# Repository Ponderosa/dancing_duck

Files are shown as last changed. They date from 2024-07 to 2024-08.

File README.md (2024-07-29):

# Dancing Duck

This repo contains all software and tools for the Dancing Duck installation (title subject to change) for the Bumbershoot 2024 Festival. 

- Duck Firmware (Foundational work complete - RTOS, WiFi, MQTT Messaging, JSON interpretation, and Motor Control)
- Coordinator (Mosquitto is functionally passing motor command messages to duck)
- Monitor (No progress)

The design consists of ~20 motorized ducks that can be controlled to perform coordinated dance moves in the water. The ducks are decoys with an RC hobby boat mounted to the bottom. There are two DC brushed motor, each attached to a propeller. A custom PCBA will be manufactured that will feature the rPi Pico and a TI DRV33xx chip. The multicore RP2040 will be running SMP FreeRTOS and include LwIP and MQTT stacks. It will be able to interface with the Coordinator MQTT broker to receive motor commands, which will interface with a TI 83xx driver chip. Also included is a magnetometer to help ducks point in desired directions and to return to dock when needed.  

The ducks will be controlled via MQTT text based instructiones (JSON, G-Code, Something hand rolled?) being issued from the RPi4 Coordinator. The Coordinator will be running a broker, likely Mosquitto. Logging and monitoring infrastructure will be running on the Coordinator and may be accessed via a touchscreen mounted directly to the RPi4 or an external laptop known as the Monitor. 

# Duck Firmware
## Build Instructions
```
$ sudo apt update
$ sudo apt install cmake gcc-arm-none-eabi libnewlib-arm-none-eabi libstdc++-arm-none-eabi-newlib build-essential git
$ cd ~/workspace (or wherever you want to clone to)
$ git clone --recurse-submodules https://github.com/Ponderosa/dancing_duck.git
$ cd dancing_duck
$ git submodule update --init --recursive
$ cp wifi_example.sh wifi_secret.sh
$ vim wifi_secret.sh (add desired access point and MQTT broker information here)
$ ./build.sh <device_id>
```
Note: Please be careful not to commit any private wifi AP information.

For further Pico information, please see the getting started link below.

## Flashing Instructions
### Copy to mass storage via USB
The Pico can load firmware images by copying the U2F output file. It needs to put into mass storage mode first. To do this hold down the button on the pico while plugging in the USB cable. More instructions can be found in the getting started manual linked below.

### J-Link
1. Download and install latest package https://www.segger.com/downloads/jlink/ (Top section)
2. Solder 3 pins to Debug port on Pico and wire to SWD interface on J-Link.
3. Wire up hard reset pin to J-Link (Labeled "Run" on Pico)
4. Use flash.sh, ex `$ JLinkExe -ip 192.168.4.151 flash.sh`

### OpenOCD
Follow the getting started with Pico guide below.

## Debugging

### Serial Port
printf() is currently outputting to UART0 (GP0, GP1) at 3.3V. The UART is set to 115200-8-N-1. A lot of useful information is being streamed to this port. It is highly recommended to utilize this debug feature before venturing into GDB. 

Todo: Add build configuration file that can switch to USB CDC printf(). Or just move to USB CDC printf(). More details on CMakeLists modifications here: https://deepbluembedded.com/raspberry-pi-pico-serial-usb-c-sdk-serial-print-monitor/

### GDB
Since the rp2040 is dual core, care must be taken in properly attaching to the device. 

Included is a .vscode/launch.json to use with the VSCode plugin Cortex-Debug by marus25. Please feel free to add more configurations, as you probably don't have the same J-Link IP address I do. To get this to work start the Debug session directly from VSCode. You may need to reset the device one or two times with the left most reset button that appears in the new toolbar in the center top of VSCode. Once you do that, you should be able to use breakpoints and step through the code. 

Getting ARM GDB to run properly on Linux can be challenging. You may need to install older versions of libncurses and libncursesw

For my Ubuntu build this did the trick
```
sudo apt-get install libncurses5
sudo apt-get install libncursesw5
```

## Pico Documentation
- https://www.raspberrypi.com/documentation/microcontrollers/raspberry-pi-pico.html
- https://datasheets.raspberrypi.com/pico/getting-started-with-pico.pdf
- https://datasheets.raspberrypi.com/pico/raspberry-pi-pico-c-sdk.pdf
- https://datasheets.raspberrypi.com/rp2040/rp2040-datasheet.pdf

# Coordinator
1. Install https://mosquitto.org/download/ on RPi4.
2. edit `etc/mosquitto/conf.d/mosquitto.conf` and add 
```
allow_anonymous true
listener 1883 0.0.0.0
```
3. Run https://mqttx.app/ on any machine in the network for monitoring.

# MQTT Topics WIP
```
dancing_duck/
├── devices/
│   ├── {device_id}/
│   │   ├── sensors/
│   │   │   ├── temperature
│   │   │   ├── battery_voltage
│   │   │   └── ...
│   │   ├── metrics/
│   │   │   ├── freertos/
│   │   │   │   ├── heap
│   │   │   │   ├── tasks
│   │   │   │   └── ...
│   │   │   └── lwip
│   │   └── logs/
│   │   |   ├── info
│   │   |   ├── warning
│   │   |   └── error
│   │   └── command/
│   │   |   ├── motor
│   │   |   ├── navigate
│   │   |   ├── return_to_dock
│   │   |   ├── set_test_mode
│   │   |   └── ...
│   │   └── quack
│   └── ...
└── all_devices/
    ├── status
    └── command
        └── uart_tx
```

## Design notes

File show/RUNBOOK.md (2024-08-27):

# Bumbershoot 2024 Runbook

## Show

### Hook up phone to network
- Get wifi network and password from team lead once on site.
- Turn off 5G on phone (you will not have internet access or receive calls during this time)
- Visit http://192.168.42.2:3000/d/cdtmyrxqlji80b/duck-dance-party?orgId=1
- Get username and password from lead.
- Once done checking dashboards, re-enable 5G so you can operate your phone normally. 

### Stuck Duck
- If possible check propellers for fouling such as feathers, refuse, or others.
  - Gently remove fouling
  - Double check drain is secure plugged in
  - Return to water by pushing the duck off towards the center
- Check battery voltage for particular duck in Grafana dashboards
  - Disable 5G
  - Visit http://192.168.42.2:3000/d/cdtmyrxqlji80b/duck-dance-party?orgId=1
  - Scroll to "Duck - System" row
  - Select proper device
  - If below 4V (device 1 battery sense doesn't work)
    - Retrieve duck if posssible, remove batteries, and contatct team lead for debug
- If we are not receiving metrics from duck for more than 15 minutes and duck is not moving for more than 5 minutes
  -  Retrieve duck if possible, remove batteries, and contact team lead for debug

### Wind clumping
1. Enable wind correction with CLI
  1. Identify wind direction
  2. `python3 duck_mqtt_cli.py wind_on -d <direction of wind in degrees> -t <time in seconds to correct for wind> -i <interval in seconds>`
  3. Try using launch time for duration and 5 to 15 minutes for interval

## Setup
### Pre-show Preperation
1. Take a picture of each duck with respective boat for debugging
1. Enable hotspot on phone to synchronize rpi4 clock 
1. Enable power to command station
1. Wait for wi-fi to initialize
1. Log into Grafana to check rpi4 metrics
1. Calibrate and launch all ducks
1. SSH into server and start show
   1. `cd workspace/dancing_duck/show`
   1. `./run_show.sh`

### Duck Launch
1. Add fresh batteries to boat and secure battery cover
1. Setup boat on calibration platform
1. Use CLI to send calibration command 
   1. `cd show`
   2. `python3 duck_mqtt_cli.py device <n> calibrate`
   3. Rotate boat slowly on calibration platform
1. Attach duck decoy to boat
1. Launch Duck
   1. Place duck in water
   1. Identify heading towards center of pool
   1. `python3 duck_mqtt_cli.py device <n> launch --heading <0-359> --launch_time <10-100>`
   1. Adjust launch time on next duck to approximately get to center of pool

### Teardown
1. Remove all batteries from all duck and place each set of batteries in it's own baggie.

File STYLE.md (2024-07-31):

## File Format
- Use format on save.
- The .clang-format file found in this directory will be used.
- It uses the Google style with longer line limits and some macro readability improvements. 
- This file is not set in stone, please feel free to suggest updates.
- Do not let a file length exceed 1000 lines. Consider refactor at 500 lines.

## Parenthesis
- Use them everywhere. Assume the other person reading the code doesn't know operator precedence. 

## Keywords to frequent
- static
- const
- volatile (where appropriate)
- double (avoid 32-bit float issues)

## Typedefs
- Generally avoid typedefs
- Do not use for structs or enums
- Allowed for fixed width integer types (more below)

## Interger representation
- Use fixed width integer type almost always. Ex `uint32_t foo = 42;`
- Use fixed width macros for string formatting. Ex `printf("Number: %" PRIu32 "\n", number);`
- Using `int` is fine for loops unless you are explictly relying on the rollover

## String formatting
- All string formatting will use `snprintf()` unless there is a good reason not to.
- Exception: using printf is fine for simple string formatting.

## Functions
- Generally keep functions less than 50 lines
- Exception: Long case statements, where each case is only a couple lines of code
- Keep local variable to less then 5~10
- Keep indentation level low. Invert your logic and split your loops if needed. 

## Function Prototypes
- Keep variable names and types

## Early exits and jumps
- Try to only have one return statement per function. There are exceptions.
- When using early exits or jumps clearly label where they happen in code
- Give jumps descriptive names
- Note: Jumps are usually for cleaning up memory allocation for early exits

## Braces
- Always use them, even for one line if statements

## Commenting
- Describe What code does, sometimes Why, and not How it works.
- Describe all public interfaces in header files
- Do not comment out large sections of code, if needed for testing wrap in if statement and add config variable
- Todo: Should this project use doxygen type comments?

## Macros
- Avoid `#define constant`, and use `static type name = val` instead.
- Use enums when defining related constants
- Macros with multiple statements should use a do while loop to protect them
- Macros should not effect control flow (very bad)
- Functions are preferred to macros if equivelency can be made

## Naming 
- Use descriptive naming for any global variables or interfaces
- Use descriptive naming when in doubt
- Exceptions are loop counters and internal variables to short functions
- Excpetion: Anytime when interacting with library, such as FreeRTOS, the naming convention of that library may bleed into this project. We are working with multiple libraries and cannot just inherit one style.

### Modules
- .c and .h files should be snake case (all_lower_case_with_underscores)

### Functions
- Functions should snake case (all_lower_case_with_underscores)
- Functions returning a value with units should be postfixed with the unit they are returning i.e. `uint32_t get_time_ms()`
- Exception: FreeRTOS task functions shall follow FreeRTOS naming conventions `vFreeRTOSTask`

### Types
- For enums, structs, typedefs(used judicially), etc, use upper camel case (UpperCamelCase)

### Macros
- If you absolutely have to use a macro, use UPPER_CASE naming convention

### Static Const for #define replacement
- Same as macros, UPPER_CASE

### Variables
- All variable names shall use snake_case unless otherwise called out below
- enum variables shall use the UPPER_CASE naming convention, make sure you don't create collisions with macros
- Variables should always end with their units if they are a measure of something (`float magnetic_flux_uT = 0;` - micro Tesla)
- Capital letters are allowed for units. For very common units like seconds, keep them lower case.
- Prefix gloabl variables with global `char global_mac_address[32]`
- Try to avoid use of global variables.

## Allocating memory
- The FreeRTOS memory allocator is preferred.

## Casting
- Cast away from void* as soon as possible
- If casting, ask yourself if the original type should change 

## Zeroing memory
- use {0} when defining, otherwise use memset

## Early optimization
- Don't inline functions unless you have data to support it's use
- If the task stack watermark is less than half, make it larger
  - Exception: We start to approach 70% max heap usage watermark
- Only use floats, instead of doubles, if optimization calls for it
- Only use fixed point math if optimization calls for it

## Conditional Compilation
- Try to avoid in general
- Leave a comment at the end of #endif 

## Resetting the device and panicking
- Try to avoid this and fail gracefully
- Exceptions, if we can not connect to wi-fi we are dead in the water.
  - Todo: consider auto return to dock if we loose wi-fi after multiple reboots and still have the compass

## Inspriation for this Guide
- Personal Experience - Style guides are highly opinionated
- Linux kernel coding style https://www.kernel.org/doc/html/latest/process/coding-style.html
- Barr's Embedded C Coding Standard https://barrgroup.com/embedded-systems/books/embedded-c-coding-standard
- Ben Klemens, 21st Century C
- Google C++ Style Guide https://google.github.io/styleguide/cppguide.html

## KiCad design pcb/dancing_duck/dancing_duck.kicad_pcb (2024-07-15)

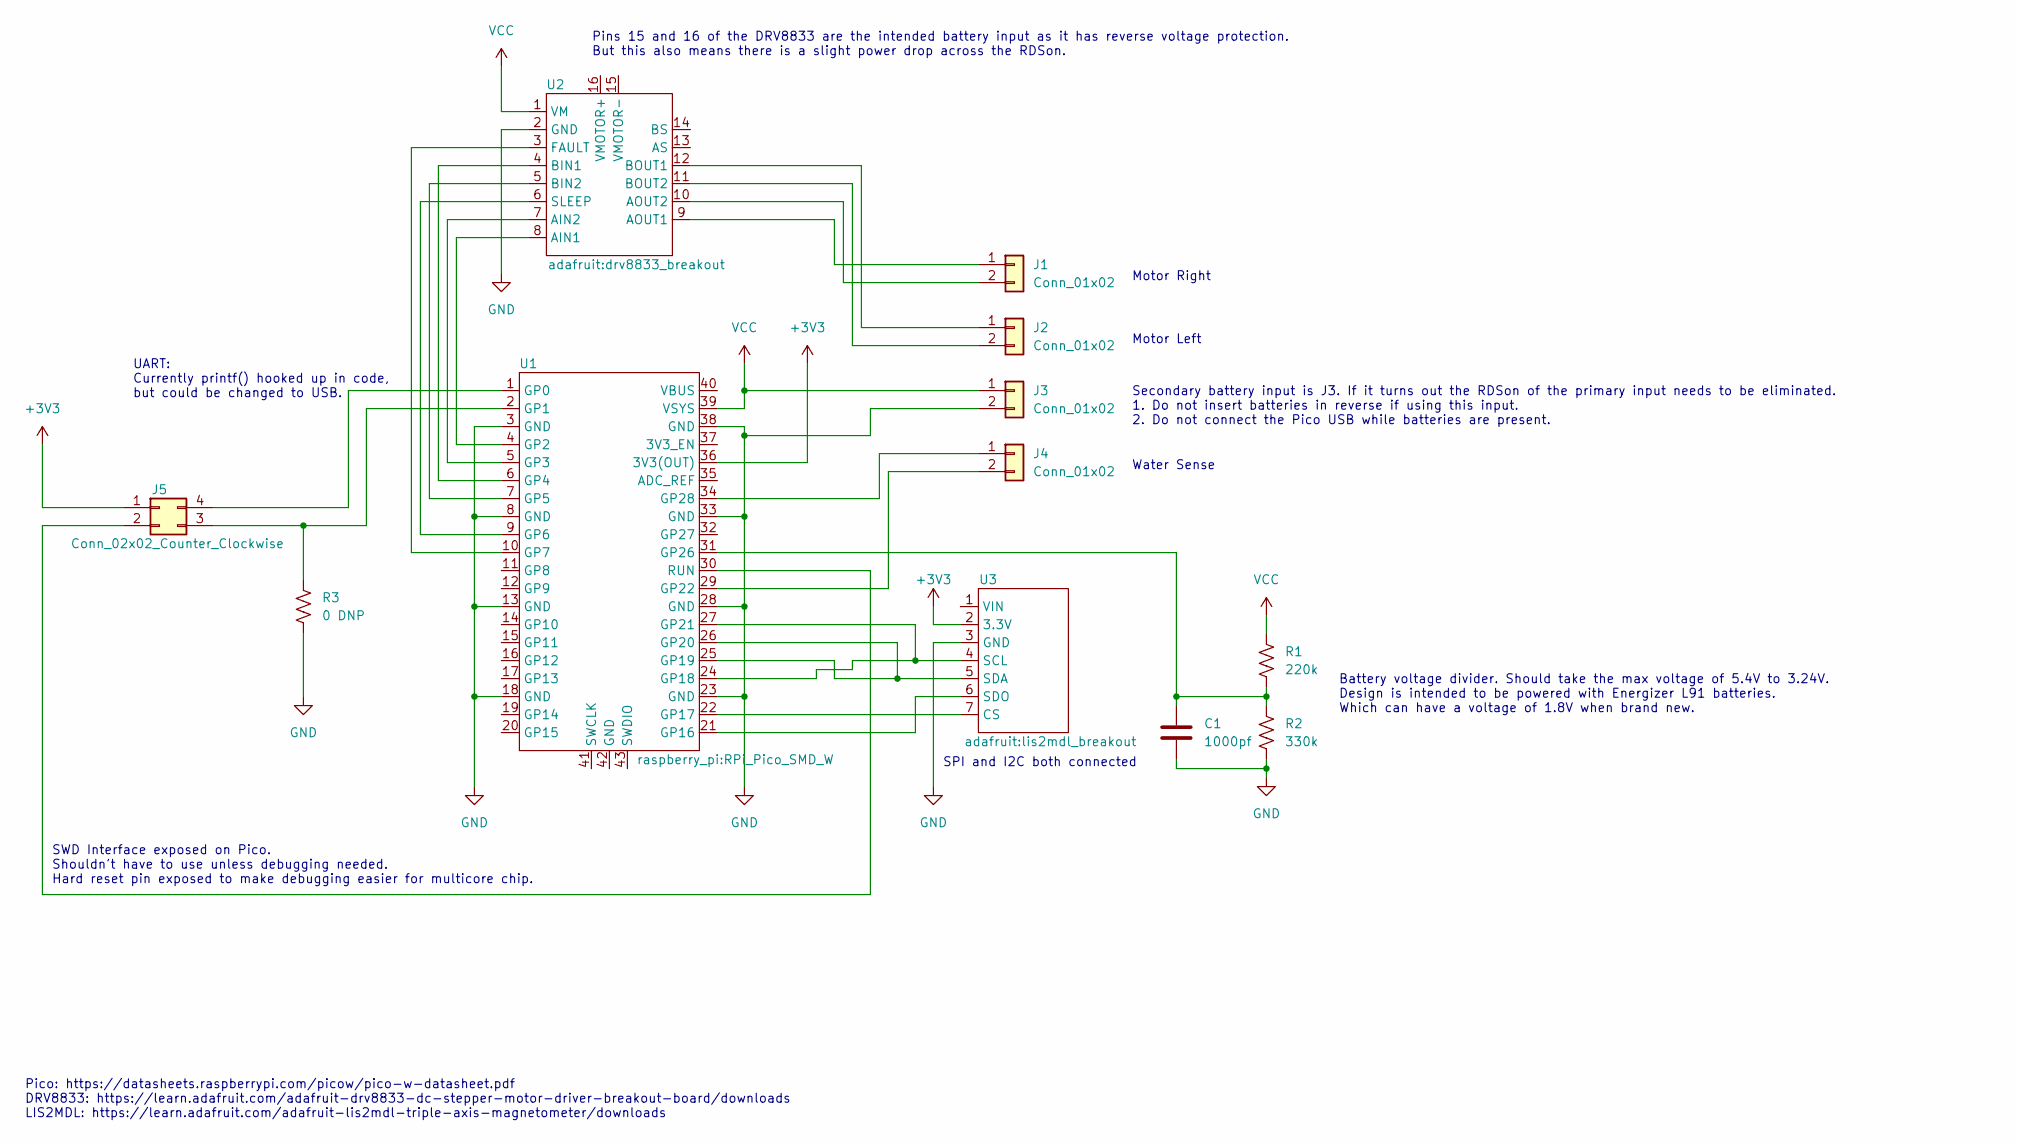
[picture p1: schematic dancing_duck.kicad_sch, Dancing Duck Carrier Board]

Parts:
C1: 1000pf; C_1206_3216Metric_Pad1.33x1.80mm_HandSolder; Part Num CL31B102KGFNNNE
J1, J2, J4: Conn_01x02; JST_PH_S2B-PH-K_1x02_P2.00mm_Horizontal
J3: Conn_01x02; TerminalBlock_Phoenix_PT-1,5-2-3.5-H_1x02_P3.50mm_Horizontal
J5: Conn_02x02_Counter_Clockwise; PinHeader_2x02_P2.54mm_Vertical
R1: 220k; R_1206_3216Metric_Pad1.30x1.75mm_HandSolder
R2: 330k; R_1206_3216Metric_Pad1.30x1.75mm_HandSolder
R3: 0 DNP; SolderJumper-2_P1.3mm_Open_TrianglePad1.0x1.5mm
U1: RPi_Pico_SMD_W
U2: drv8833_breakout
U3: lis2mdl_breakout

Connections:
+3V3: J5.1, U1.36 (3V3(OUT)), U3.2 (3.3V)
GND: C1.2, J3.2, R2.2, R3.2, U1.3 (GND), U1.8 (GND), U1.13 (GND), U1.18 (GND), U1.23 (GND), U1.28 (GND), U1.33 (GND), U1.38 (GND), U2.2 (GND), U3.3 (GND)
unnamed: J1.1, U2.9 (AOUT1)
unnamed: J1.2, U2.10 (AOUT2)
unnamed: J2.1, U2.12 (BOUT1)
unnamed: J2.2, U2.11 (BOUT2)
unnamed: J4.1, U1.34 (GP28)
unnamed: J4.2, U1.29 (GP22)
unnamed: J5.2, U1.30 (RUN)
unnamed: J5.3, R3.1, U1.2 (GP1)
unnamed: J5.4, U1.1 (GP0)
unnamed: U1.4 (GP2), U2.8 (AIN1)
unnamed: U1.5 (GP3), U2.7 (AIN2)
unnamed: U1.6 (GP4), U2.4 (BIN1)
unnamed: U1.7 (GP5), U2.5 (BIN2)
unnamed: U1.9 (GP6), U2.6 (SLEEP)
unnamed: U1.10 (GP7), U2.3 (FAULT)
unnamed: U1.21 (GP16), U3.6 (SDO)
unnamed: U1.22 (GP17), U3.7 (CS)
unnamed: U1.24 (GP18), U1.27 (GP21), U3.4 (SCL)
unnamed: U1.25 (GP19), U1.26 (GP20), U3.5 (SDA)
unnamed: C1.1, R1.2, R2.1, U1.31 (GP26)
VCC: J3.1, R1.1, U1.39 (VSYS), U2.1 (VM)

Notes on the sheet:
Motor Right
Motor Left
Secondary battery input is J3. If it turns out the RDSon of the primary input needs to be eliminated. 1. Do not insert batteries in reverse if using this input. 2. Do not connect the Pico USB while batteries are present.
Water Sense
Pico: https://datasheets.raspberrypi.com/picow/pico-w-datasheet.pdf DRV8833: https://learn.adafruit.com/adafruit-drv8833-dc-stepper-motor-driver-breakout-board/downloads LIS2MDL: https://learn.adafruit.com/adafruit-lis2mdl-triple-axis-magnetometer/downloads
Battery voltage divider. Should take the max voltage of 5.4V to 3.24V. Design is intended to be powered with Energizer L91 batteries. Which can have a voltage of 1.8V when brand new.
UART: Currently printf() hooked up in code, but could be changed to USB.
Pins 15 and 16 of the DRV8833 are the intended battery input as it has reverse voltage protection. But this also means there is a slight power drop across the RDSon.
SPI and I2C both connected
SWD Interface exposed on Pico. Shouldn't have to use unless debugging needed. Hard reset pin exposed to make debugging easier for multicore chip.

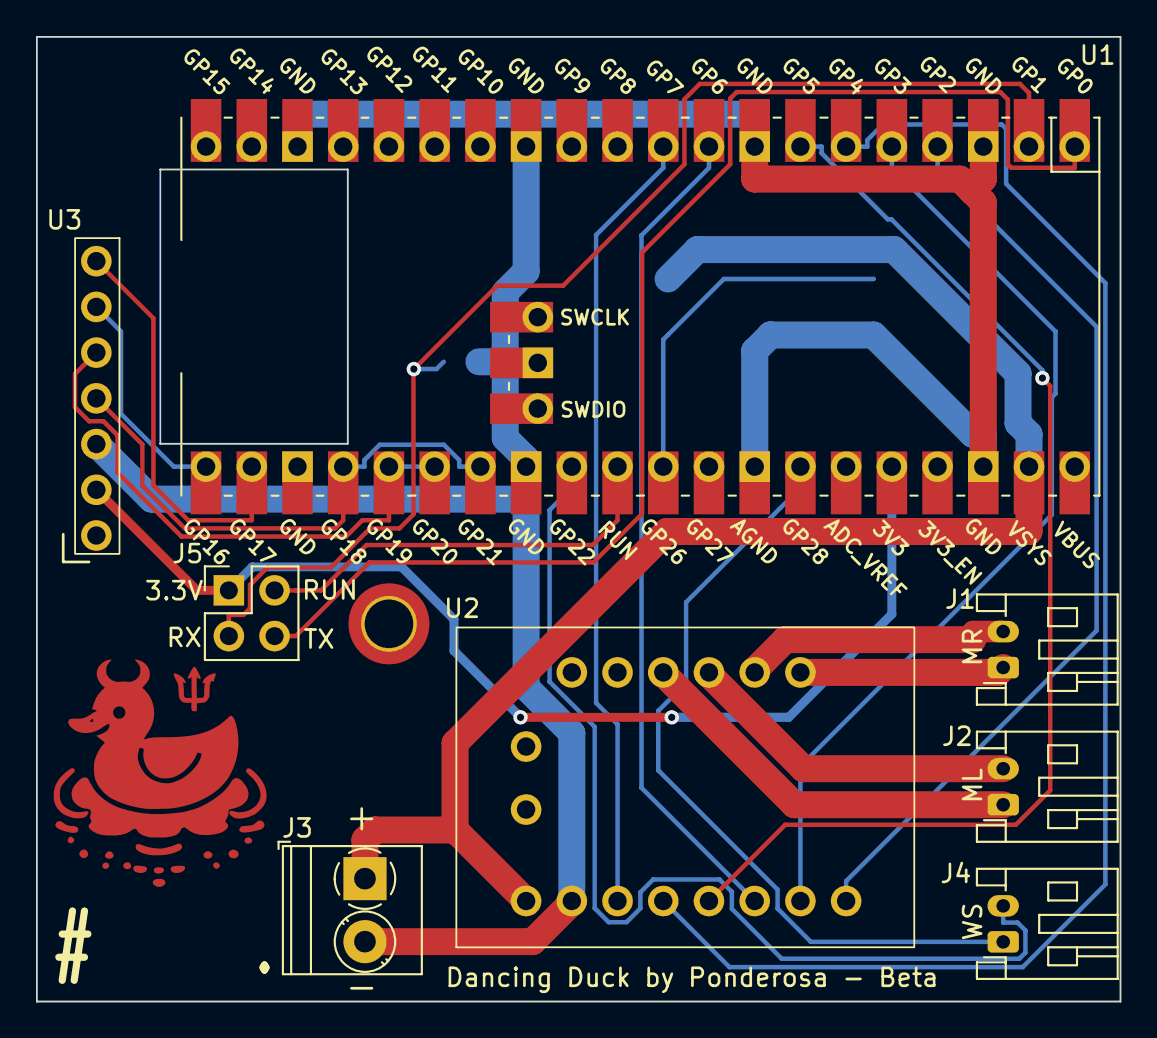
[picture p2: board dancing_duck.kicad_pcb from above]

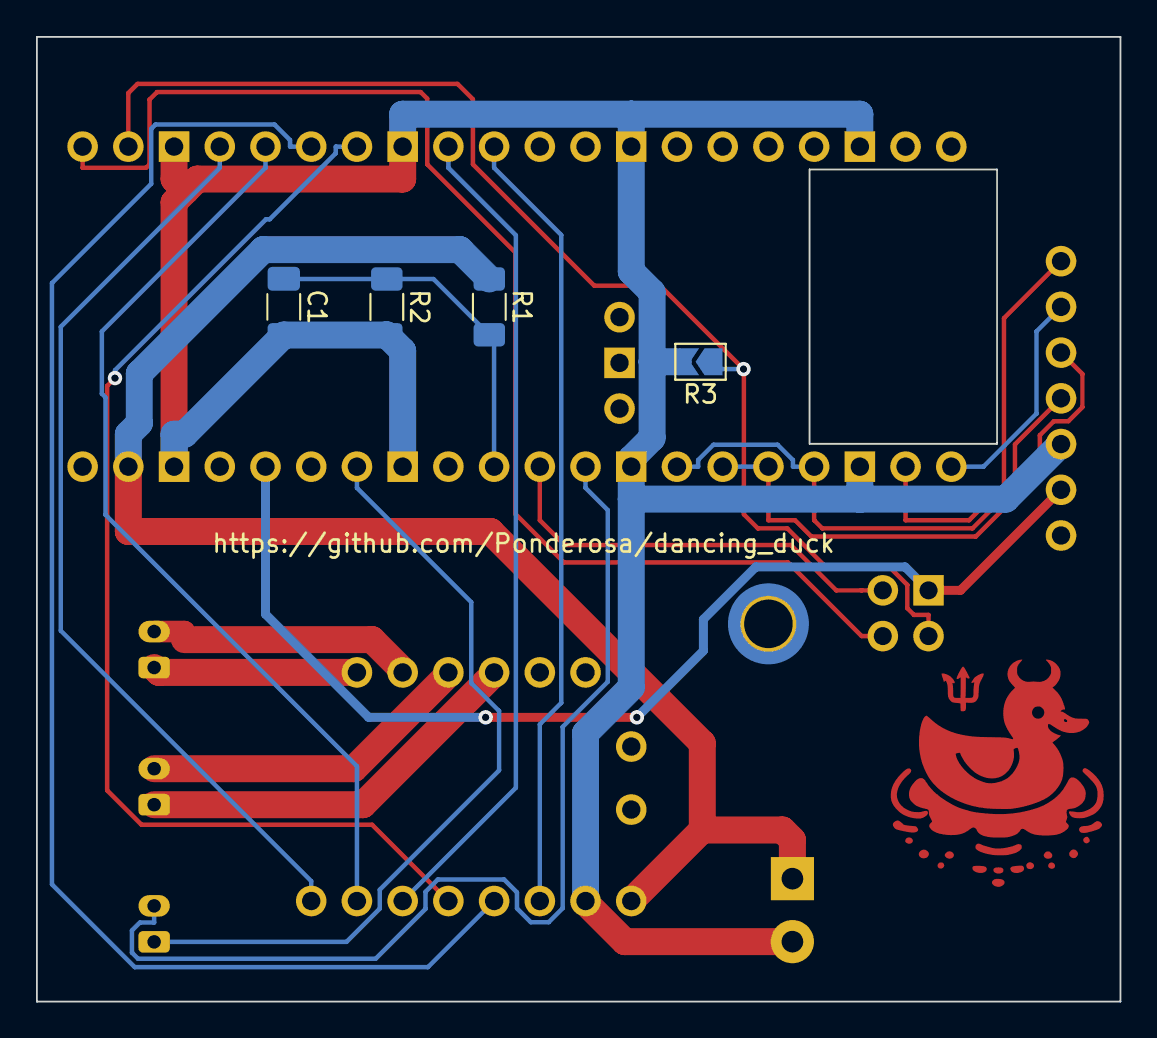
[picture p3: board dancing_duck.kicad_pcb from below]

Board: 2 copper layers, 60.2 x 53.6 mm, 14 parts (4 on the bottom side), 23 nets.

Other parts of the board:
G_LOGO: LOGO
REF1: MountingHole_2.7mm_M2.5_ISO14580_Pad_TopBottom

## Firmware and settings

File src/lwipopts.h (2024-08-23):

#ifndef _LWIPOPTS_H
#define _LWIPOPTS_H

// Common settings used in most of the pico_w examples
// (see https://www.nongnu.org/lwip/2_1_x/group__lwip__opts.html for details)

// allow override in some examples
#ifndef NO_SYS
#define NO_SYS 0
#endif
// allow override in some examples
#ifndef LWIP_SOCKET
#define LWIP_SOCKET 1
#endif
#if PICO_CYW43_ARCH_POLL
#define MEM_LIBC_MALLOC 1
#else
// MEM_LIBC_MALLOC is incompatible with non polling versions
#define MEM_LIBC_MALLOC 0
#endif
#define MEM_ALIGNMENT              4
#define MEM_SIZE                   4000
#define MEMP_NUM_TCP_SEG           32
#define MEMP_NUM_ARP_QUEUE         10
#define MEMP_NUM_SYS_TIMEOUT       (LWIP_NUM_SYS_TIMEOUT_INTERNAL + 2)
#define PBUF_POOL_SIZE             24
#define LWIP_ARP                   1
#define LWIP_ETHERNET              1
#define LWIP_ICMP                  1
#define LWIP_RAW                   1
#define TCP_WND                    (8 * TCP_MSS)
#define TCP_MSS                    1460
#define TCP_SND_BUF                (8 * TCP_MSS)
#define TCP_SND_QUEUELEN           ((4 * (TCP_SND_BUF) + (TCP_MSS - 1)) / (TCP_MSS))
#define LWIP_NETIF_STATUS_CALLBACK 1
#define LWIP_NETIF_LINK_CALLBACK   1
#define LWIP_NETIF_HOSTNAME        1
#define LWIP_NETCONN               0
#define MEM_STATS                  0
#define SYS_STATS                  0
#define MEMP_STATS                 0
#define LINK_STATS                 0
// #define ETH_PAD_SIZE                2
#define LWIP_CHKSUM_ALGORITHM      3
#define LWIP_DHCP                  1
#define LWIP_IPV4                  1
#define LWIP_TCP                   1
#define LWIP_UDP                   1
#define LWIP_DNS                   1
#define LWIP_TCP_KEEPALIVE         1
#define LWIP_NETIF_TX_SINGLE_PBUF  1
#define DHCP_DOES_ARP_CHECK        0
#define LWIP_DHCP_DOES_ACD_CHECK   0

#ifndef NDEBUG
#define LWIP_DEBUG         1
#define LWIP_STATS         1
#define LWIP_STATS_DISPLAY 1
#endif

#define ETHARP_DEBUG     LWIP_DBG_OFF
#define NETIF_DEBUG      LWIP_DBG_OFF
#define PBUF_DEBUG       LWIP_DBG_OFF
#define API_LIB_DEBUG    LWIP_DBG_OFF
#define API_MSG_DEBUG    LWIP_DBG_OFF
#define SOCKETS_DEBUG    LWIP_DBG_OFF
#define ICMP_DEBUG       LWIP_DBG_OFF
#define INET_DEBUG       LWIP_DBG_OFF
#define IP_DEBUG         LWIP_DBG_OFF
#define IP_REASS_DEBUG   LWIP_DBG_OFF
#define RAW_DEBUG        LWIP_DBG_OFF
#define MEM_DEBUG        LWIP_DBG_OFF
#define MEMP_DEBUG       LWIP_DBG_OFF
#define SYS_DEBUG        LWIP_DBG_OFF
#define TCP_DEBUG        LWIP_DBG_OFF
#define TCP_INPUT_DEBUG  LWIP_DBG_OFF
#define TCP_OUTPUT_DEBUG LWIP_DBG_OFF
#define TCP_RTO_DEBUG    LWIP_DBG_OFF
#define TCP_CWND_DEBUG   LWIP_DBG_OFF
#define TCP_WND_DEBUG    LWIP_DBG_OFF
#define TCP_FR_DEBUG     LWIP_DBG_OFF
#define TCP_QLEN_DEBUG   LWIP_DBG_OFF
#define TCP_RST_DEBUG    LWIP_DBG_OFF
#define UDP_DEBUG        LWIP_DBG_OFF
#define TCPIP_DEBUG      LWIP_DBG_OFF
#define PPP_DEBUG        LWIP_DBG_OFF
#define SLIP_DEBUG       LWIP_DBG_OFF
#define DHCP_DEBUG       LWIP_DBG_OFF

#if !NO_SYS
#define TCPIP_THREAD_STACKSIZE        6144
#define DEFAULT_THREAD_STACKSIZE      1024
#define DEFAULT_RAW_RECVMBOX_SIZE     8
#define TCPIP_MBOX_SIZE               8
#define LWIP_TIMEVAL_PRIVATE          0
#define TCPIP_THREAD_PRIO             20

// not necessary, can be done either way
#define LWIP_TCPIP_CORE_LOCKING_INPUT 1

// ping_thread sets socket receive timeout, so enable this feature
#define LWIP_SO_RCVTIMEO              1
#endif

// MQTT
#define MQTT_REQ_MAX_IN_FLIGHT 64

#endif /* __LWIPOPTS_H__ */

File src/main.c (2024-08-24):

#include <inttypes.h>

#include "FreeRTOS.h"

#include "pico/cyw43_arch.h"
#include "pico/stdlib.h"

#include "adc.h"
#include "blink.h"
#include "commanding.h"
#include "config.h"
#include "dance_generator.h"
#include "dance_time.h"
#include "hardware/watchdog.h"
#include "magnetometer.h"
#include "motor.h"
#include "mqtt.h"
#include "picowota/reboot.h"
#include "publish.h"
#include "reboot.h"
#include "task.h"
#include "watchdog.h"
#include "wifi.h"

// Local Variables
static const bool FREERTOS_PRINT_INFO_DEBUG = false;  // Debug only! Causes long scheduler holds
static mqtt_client_t static_client;

// Global Variables
char global_mac_address[32];

// Local Functions
static void print_task_information(const TaskStatus_t *task_status_array, size_t array_size) {
  printf("\n");
  printf("%-20s %-10s %-10s %-20s %-10s\n", "Task Name", "State", "Priority",
         "Stack Low Water Mark", "Task Number");

  for (UBaseType_t i = 0; i < array_size; i++) {
    printf("%-20s %-10" PRIu32 " %-10" PRIu32 " %-20" PRIu32 " %-10" PRIu32 "\n",
           task_status_array[i].pcTaskName, (uint32_t)task_status_array[i].eCurrentState,
           task_status_array[i].uxCurrentPriority, task_status_array[i].usStackHighWaterMark,
           task_status_array[i].xTaskNumber);
  }
}

static void print_heap_information() {
  size_t minimum_heap_size = xPortGetMinimumEverFreeHeapSize();

  printf("\n");
  printf("Heap Info:\n");
  printf("Maximum Free: %" PRIu32 " bytes\n", (uint32_t)configTOTAL_HEAP_SIZE);
  printf("Current Free: %" PRIu32 " bytes\n", (uint32_t)xPortGetFreeHeapSize());
  printf("Minimum Free: %" PRIu32 " bytes\n", (uint32_t)minimum_heap_size);
  printf("Max %% Used  : %.2f%%\n",
         100.0 * (1.0 - (double)minimum_heap_size / (double)configTOTAL_HEAP_SIZE));
}

// Print FreeRTOS stats periodically - Debug Only
static void vFreeRTOSInfoTask() {
  UBaseType_t uxArraySize;
  TaskStatus_t *pxTaskStatusArray;

  vTaskDelay(1000);

  for (;;) {
    print_heap_information();

    uxArraySize = uxTaskGetNumberOfTasks();
    pxTaskStatusArray = pvPortMalloc(uxArraySize * sizeof(TaskStatus_t));

    if (pxTaskStatusArray != NULL) {
      uxArraySize = uxTaskGetSystemState(pxTaskStatusArray, uxArraySize, NULL);
      print_task_information(pxTaskStatusArray, uxArraySize);

      vPortFree(pxTaskStatusArray);
    } else {
      printf("Memory allocation failed.\n");
    }

    vTaskDelay(15000);
  }
}

static void wifi_connect() {
  printf("Connecting to Wi-Fi...\n");
  if (PRINT_WIFI_CREDS) {
    printf("WiFi SSID: %s\n", WIFI_SSID);
    printf("WiFI Password: %s\n", WIFI_PASSWORD);
  }

  bool connected = false;

  for (int i = 0; i < WIFI_CONNECT_RETRY_COUNT; i++) {
    if (cyw43_arch_wifi_connect_timeout_ms(WIFI_SSID, WIFI_PASSWORD, CYW43_AUTH_WPA2_AES_PSK,
                                           WIFI_TIMEOUT_MS)) {
      printf("failed to connect to wifi.\n");
      watchdog_update();
    } else {
      printf("Connected.\n");
      connected = true;
      break;
    }
  }
  if (!connected) {
    // Todo: consider return to dock
    reboot(WIFI_CONNECT_REASON);
  }
}

// This task as early exits! Be careful with allocation.
static void vInitTask() {
  // WiFi chip init - Must be ran in FreeRTOS Task
  if (cyw43_arch_init()) {
    printf("Wi-Fi init failed\n");
    // Todo: consider return to dock
    reboot(WIFI_INIT_REASON);
  } else {
    printf("Wi-Fi init passed!\n");
  }

  // Init task must manage watchdog
  watchdog_update();

  // Enable "Station" mode (as opposed to Access Point)
  cyw43_arch_enable_sta_mode();

  // Modes other than MQTT are for bringup and debug
  switch (WIFI_MODE) {
    case MQTT:
      wifi_connect();
      break;
    case PING:
      wifi_connect();
      xTaskCreate(vPing, "Ping Task", 2048, NULL, 3, NULL);
      vTaskDelete(NULL);  // Delete the current task ! EARLY EXIT !
      break;
    case SCAN:
      xTaskCreate(vScanWifi, "Scan Wifi Task", 2048, NULL, 2, NULL);
      vTaskDelete(NULL);  // Delete the current task ! EARLY EXIT !
      break;
    default:
      printf("Error: WIFI_MODE misconfigured!");
      vTaskDelete(NULL);  // Delete the current task ! EARLY EXIT !
  }

  // Init task must manage watchdog
  watchdog_update();

  // Print MAC address
  uint8_t mac[6];
  cyw43_wifi_get_mac(&cyw43_state, CYW43_ITF_STA, mac);
  snprintf(global_mac_address, 18, "%02X:%02X:%02X:%02X:%02X:%02X", mac[0], mac[1], mac[2], mac[3],
           mac[4], mac[5]);
  printf("MAC: %s\n", global_mac_address);

  // FreeRTOS Shared Resources
  QueueHandle_t motor_queue = xQueueCreate(MOTOR_QUEUE_DEPTH, sizeof(struct MotorCommand));
  if (!motor_queue) {
    printf("Motor Queue Creation failed!\n");
  }

  QueueHandle_t duck_mode_mailbox = xQueueCreate(1, sizeof(enum DuckMode));
  if (!duck_mode_mailbox) {
    printf("Duck Mode Mailbox Creation Failed!\n");
  }

  QueueHandle_t mag_mailbox = xQueueCreate(1, sizeof(struct MagXYZ));
  if (!mag_mailbox) {
    printf("Mag Mailbox Creation Failed!\n");
  }

  QueueHandle_t wind_mailbox = xQueueCreate(1, sizeof(struct WindCorrection));
  if (!wind_mailbox) {
    printf("Wind Mailbox Creation Failed!\n");
  }

  SemaphoreHandle_t motor_stop_semaphore = xSemaphoreCreateBinary();
  if (!motor_stop_semaphore) {
    printf("Motor Semaphore Creation failed!\n");
  }

  SemaphoreHandle_t calibration_semaphore = xSemaphoreCreateBinary();
  if (!calibration_semaphore) {
    printf("Calibration Semaphore Creation failed!\n");
  }

  // Set Duck Mode
  enum DuckMode dm = DRY_DOCK;
  if (calibration_data_found()) {
    dm = DANCE;
  }
  xQueueOverwrite(duck_mode_mailbox, &dm);

  // Assemble shared resource
  struct MagnetometerTaskParameters *mag_params =
      (struct MagnetometerTaskParameters *)pvPortMalloc(sizeof(struct MagnetometerTaskParameters));
  mag_params->mag_mailbox = mag_mailbox;
  mag_params->calibrate = calibration_semaphore;

  struct MotorTaskParameters *motor_params =
      (struct MotorTaskParameters *)pvPortMalloc(sizeof(struct MotorTaskParameters));
  motor_params->command_queue = motor_queue;
  motor_params->mag_queue = mag_mailbox;
  motor_params->motor_stop = motor_stop_semaphore;

  struct PublishTaskParameters *publish_params =
      (struct PublishTaskParameters *)pvPortMalloc(sizeof(struct PublishTaskParameters));
  publish_params->client = &static_client;
  publish_params->mag = mag_mailbox;
  publish_params->duck_mode_mailbox = duck_mode_mailbox;

  struct MqttParameters *mqtt_params =
      (struct MqttParameters *)pvPortMalloc(sizeof(struct MqttParameters));
  mqtt_params->motor_queue = motor_queue;
  mqtt_params->duck_mode_mailbox = duck_mode_mailbox;
  mqtt_params->wind_mailbox = wind_mailbox;
  mqtt_params->motor_stop = motor_stop_semaphore;
  mqtt_params->calibrate = calibration_semaphore;

  struct DanceTimeParameters *dance_params =
      (struct DanceTimeParameters *)pvPortMalloc(sizeof(struct DanceTimeParameters));
  dance_params->motor_queue = motor_queue;
  dance_params->duck_mode_mailbox = duck_mode_mailbox;
  dance_params->wind_mailbox = wind_mailbox;

  // FreeRTOS Task Creation - Lower number is lower priority!
  xTaskCreate(vBlinkTask, "Blink Task", 512, NULL, 1, NULL);
  xTaskCreate(vMagnetometerTask, "Mag Task", 2048, (void *)mag_params, 10, NULL);
  xTaskCreate(vMotorTask, "Motor Task", 512, (void *)motor_params, 11, NULL);
  xTaskCreate(vDanceTimeTask, "Dance Task", 512, (void *)dance_params, 12, NULL);
  if (mqtt_connect(&static_client, (void *)mqtt_params) == ERR_OK) {
    xTaskCreate(vPublishTask, "MQTT Pub Task", 1024, (void *)publish_params, 3, NULL);
  }
  if (FREERTOS_PRINT_INFO_DEBUG) {
    xTaskCreate(vFreeRTOSInfoTask, "Print Status Task", 512, NULL, 2, NULL);
  }
  TaskHandle_t xHandle;
  xTaskCreate(vWatchDogTask, "Watchdog Task", 128, NULL, 1, &(xHandle));
  if (DEBUG_IDLE) {
    // Toggle for CPU utilization on Logic Analyzer
    vTaskCoreAffinitySet(xHandle, 0x01);
    xTaskCreate(vToggleTask, "Toggle Task", 128, NULL, 1, &(xHandle));
    vTaskCoreAffinitySet(xHandle, 0x02);
  }

  /*
   * There are two hidden tasks in addition to the usual FreeRTOS tasks.
   * One is the pico async_context task, and the other is the tcp_ip task from LWIP.
   * The async_context_task parameters can be overridden in CMakeLists. Ex. CYW43_TASK_PRIORITY=21.
   * The LWIP task parameters can be updated in lwipopts.h. Ex. #define TCPIP_THREAD_PRIO 20
   * Note: Their are two IDLE tasks, one for each core. And only one timer service task.
   */

  printf("Init Task Complete\n");

  // Delete the current task
  vTaskDelete(NULL);
}

int main() {
  enable_watchdog();
  stdio_uart_init();

  // Init run pin override
  gpio_init(22);
  gpio_set_dir(22, GPIO_OUT);
  gpio_put(22, 1);

  init_adc();

  // Check boot reason and increment boot counter
  on_boot();

  printf("Duck ID = %" PRIu32 "\n", (uint32_t)DUCK_ID_NUM);

  // Wifi init must happen in task
  xTaskCreate(vInitTask, "Init Task", 2048, NULL, 1, NULL);
  vTaskStartScheduler();
}

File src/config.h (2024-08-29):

#ifndef _DD_CONFIG_H
#define _DD_CONFIG_H

// Firmware Version
static const uint32_t FIRMWARE_VERSION = 10;

// Watchdog
static const uint32_t WATCHDOG_DELAY_MS = 250;
static const uint32_t WATCHDOG_TIMEOUT_MS = 8000; /* Do not exceed 8333 */
static const uint32_t DD_MAGIC_NUM = 0xDECAFDAD;
static const bool DEBUG_IDLE = false;

// Wifi
enum WifiMode {
  MQTT = 0,
  PING = 1,
  SCAN = 2,
};

// Duck Mode
enum DuckMode {
  DRY_DOCK,
  CALIBRATE,
  LAUNCH,
  DANCE,
  OVERRIDE,
  STOP,
};

static const enum WifiMode WIFI_MODE = MQTT;
static const uint32_t WIFI_TIMEOUT_MS = 7000; /* Ensure less than WATCHDOG_TIMEOUT_MS */
static const int32_t WIFI_CONNECT_RETRY_COUNT = 5;
static const bool PRINT_WIFI_CREDS = false;

// Blink Task
static const uint32_t BLINK_DELAY_MS = 500;
static const bool BLINK_DEBUG = 0;

// JSON
static const bool JSON_DEBUG = 0;

// FreeRTOS Resources
static const uint32_t MOTOR_QUEUE_DEPTH = 16;

// Magnetometer
static const size_t KASA_ARRAY_DEPTH = 250;  // 25 Seconds
static const size_t KASA_LOOP_COUNTER = 25;  // 2.5 second
static const double KASA_RMSE_LOWER_LIMIT = 0.1;
static const double KASA_RMSE_UPPER_LIMIT = 10.0;
// Small value to check for near-zero conditions
static const double EPSILON = 1e-10;
static const uint32_t KASA_CALIBRATION_TIME_MS = 25000;

// Motor
static const double MIN_DUTY_CYCLE = 0.7;
static const double MAX_DUTY_CYCLE = 0.9;
static const double MID_DUTY_CYCLE = (MIN_DUTY_CYCLE + MAX_DUTY_CYCLE) / 2.0;
static const double Kp = 0.01;
static const double Kd = 0.001;

#endif

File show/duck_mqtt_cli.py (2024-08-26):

import argparse
import json
import paho.mqtt.client as mqtt
import os
import sys
import time
from enum import IntEnum


class MotorCommandType(IntEnum):
    MOTOR = 0
    POINT = 1
    SWIM = 2
    FLOAT = 3


def load_config(config_file="config.json"):
    try:
        with open(config_file, "r") as f:
            config = json.load(f)

        # List of required config parameters
        required_params = [
            "device_ids",
            "Kp",
            "Kd",
            "dock_heading_degrees",
            "time_to_swim_to_dock_s",
        ]

        # Check for missing parameters
        missing_params = [param for param in required_params if param not in config]
        if missing_params:
            raise ValueError(
                f"Config file is missing the following required parameters: {', '.join(missing_params)}"
            )

        # Validate device_ids
        device_ids = config["device_ids"]
        if not device_ids or not all(
            isinstance(id, int) and id > 0 for id in device_ids
        ):
            print(
                "Warning: device_ids should be a non-empty list of positive integers."
            )

        # Validate numeric parameters
        numeric_params = ["Kp", "Kd", "dock_heading_degrees", "time_to_swim_to_dock_s"]
        for param in numeric_params:
            if not isinstance(config[param], (int, float)) or config[param] < 0:
                raise ValueError(f"'{param}' must be a non-negative number.")

        return config
    except FileNotFoundError:
        print(f"Config file '{config_file}' not found. Please ensure it exists.")
        sys.exit(1)
    except json.JSONDecodeError:
        print(f"Error decoding '{config_file}'. Please ensure it's valid JSON.")
        sys.exit(1)
    except Exception as e:
        print(f"Error in config file: {str(e)}")
        sys.exit(1)


def on_connect(client, userdata, flags, reason_code, properties=None):
    if reason_code == 0:
        print("Connected to MQTT broker")
        client.connected_flag = True
    else:
        print(f"Connection failed with code {reason_code}")
        client.connected_flag = False


def on_publish(client, userdata, mid, reason_code=None, properties=None):
    pass  # Do nothing, effectively removing the MID printout


def create_motor_message(motor_type, config, **kwargs):
    if motor_type == MotorCommandType.MOTOR:
        return {
            "type": motor_type,
            "duty_right": kwargs.get("duty_right"),
            "duty_left": kwargs.get("duty_left"),
            "dur_ms": kwargs.get("dur_ms"),
        }
    elif motor_type == MotorCommandType.POINT:
        return {
            "type": motor_type,
            "heading": kwargs.get("heading"),
            "dur_ms": kwargs.get("dur_ms"),
        }
    elif motor_type == MotorCommandType.SWIM:
        return {
            "type": motor_type,
            "Kp": kwargs.get("Kp") or config.get("Kp"),
            "Kd": kwargs.get("Kd") or config.get("Kd"),
            "heading": kwargs.get("heading"),
            "dur_ms": kwargs.get("dur_ms"),
        }
    elif motor_type == MotorCommandType.FLOAT:
        return {"type": motor_type, "dur_ms": kwargs.get("dur_ms")}
    else:
        raise ValueError(f"Unknown motor command type: {motor_type}")


def create_return_message(config):
    return {
        "type": MotorCommandType.SWIM,
        "Kp": config.get("Kp"),
        "Kd": config.get("Kd"),
        "heading": config["dock_heading_degrees"],
        "dur_ms": int(
            config["time_to_swim_to_dock_s"] * 1000
        ),  # Convert seconds to milliseconds
    }


def send_command(client, device_id, command, config, **kwargs):
    topic = f"dancing_duck/devices/{device_id}/command/{command}"

    if command in ["calibrate", "dance", "stop_all", "reset"]:
        message = None  # No message for these commands
    elif command == "launch":
        message = json.dumps(
            {"launch_time": kwargs.get("launch_time"), "heading": kwargs.get("heading")}
        )
    elif command == "motor":
        motor_type = kwargs.pop("motor_type", None)  # Remove motor_type from kwargs
        if motor_type is None:
            raise ValueError("Motor type is required for motor command")
        message = json.dumps(create_motor_message(motor_type, config, **kwargs))
    elif command == "return":
        message = json.dumps(create_return_message(config))
    else:
        raise ValueError(f"Unknown command: {command}")

    # Print the topic and message
    print(f"Publishing to topic: {topic}")
    print(f"Message content: {message}")

    qos = 0
    result = client.publish(topic, message, qos=qos)
    result.wait_for_publish()
    print(f"{command.capitalize()} command sent to device: {device_id}")
    if command == "return":
        print(f"Return heading: {config['dock_heading_degrees']} degrees")
        print(f"Return duration: {config['time_to_swim_to_dock_s']} seconds")


def load_broker_ip():
    original_dir = os.getcwd()
    os.chdir("..")

    broker_ip = None
    files_to_check = ["wifi_secret.sh", "wifi_example.sh"]
    for file_name in files_to_check:
        if os.path.exists(file_name):
            print(f"Checking {file_name} for BROKER_IP_ADDRESS...")
            with open(file_name, "r") as f:
                for line in f:
                    if "BROKER_IP_ADDRESS=" in line:
                        parts = line.split("=", 1)
                        if len(parts) == 2:
                            broker_ip = parts[1].strip().strip('"')
                            print(f"Found BROKER_IP_ADDRESS: {broker_ip}")
                            break
            if broker_ip:
                break
        else:
            print(f"File {file_name} not found.")

    os.chdir(original_dir)

    if not broker_ip:
        print("Error: BROKER_IP_ADDRESS not found in wifi_secret.sh or wifi_example.sh")
        print("Please ensure one of these files exists and contains a line like:")
        print(
            'export BROKER_IP_ADDRESS="192.168.1.100" or BROKER_IP_ADDRESS=192.168.1.100'
        )
        sys.exit(1)

    return broker_ip


def create_wind_correction_message(direction, duration, interval, enable):
    return {
        "ww_dir": (direction + 180) % 360,  # Invert direction by 180 degrees
        "dur_s": duration,
        "inter_s": interval,
        "en": 1 if enable else 0,
    }
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

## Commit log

2024-06-07 feat: initial commit
    This is the first commit for the dancing_duck rp2040 embedded code for bumbershoot 2024.
    This code uses FreeRTOS to blink a light on the CWY wifi chip, and does a wifi scan for all local access points and prints it out on the UART0 pins.
    Next steps:
    - Get multicore GDB working
    - Add README
    - Get MQTT working with WLAN
2024-06-07 fix: GDB now working in VSCode
    Steps to debug:
    1. Update or comment out IP Address of J-Link probe
    2. Build and Flash firmware
    3. Attach each configuration
    4. Reset device with leftmost button in new toolbar.
    5. May need to reset device again after hitting a breakpoint or two, but after that should be good to go.
    [main.c]
2024-06-09 fix: cwy43 wifi now using freertos
    problem: cwy code was not using freertos context. Now it is.
    note: cwy43 must be initialized in a FreeRTOS task
    [lwipopts.h, main.c]
2024-06-10 refactor: add wifi task toggle
    wifi scan and ping cannout run at the same time. added toggle to easily allow switching between modes.
2024-06-15 fix: remove coreMQTT-Agent
    The lwip package that comes with the Pico SDK has MQTT. Using this is much easier than trying to use Amazon's FreeRTOS MQTT package. Some future work will need to be done to ensure thread safety, but it shouldn't be to bad.
    Testing: Remove build folder, run build.sh, flash to device, observed blinking LED
    [main.c]
2024-06-16 feat: add basic motor control
    Testing: with DRV8833 and DC motors on duck. Damaged one motor due to water splashing onto it.
    Project Next Steps:
    Test overall strategy by mounting electronics in duck and see how long a set of energizer lithium AA batteries last with duck spinning in circles in tub.
    Code next steps:
    Hook MQTT messaging directly to motor driver. Just allow it scale pwm duty cycle and frequency for each motor.
    [main.c, motor.c]
2024-06-16 feat: added FreeRTOS task status printing
    note: the debugger isn't aware of the FreeRTOS tasks due to it not understanding the new datastructure for SMP. Todo: look into finding a fix for this.
    [main.c]
2024-06-16 feat: JSON parsing for motor command
2024-06-17 feat: hookup mqtt to pwm
2024-06-17 cleanup: updat clang-format and run
    Testing:
    - Fresh build
    - Flash to device
    - Observe blink task
2024-06-17 refactor: motor.c
    - Remove magic numbers
    - Sanitize inputs
    - Add motor driver sleep functionality
    - Hook up duration
2024-06-17 fix: fix a few compiler warnings
    [main.c, motor.c]
2024-06-28 pcb: add first draft of pcb
    [dancing_duck.dsn, dancing_duck.kicad_pcb, dancing_duck.kicad_sch]
2024-06-28 feat: add battery adc to pcb
    [dancing_duck.kicad_pcb, dancing_duck.kicad_sch]
2024-06-28 test: add simple mqtt test to make motors wiggle
2024-06-30 doc: update schematic
    [dancing_duck.kicad_sch]
2024-07-01 feat: add bi-direction motor control
2024-07-06 feat: add magnetometer
2024-07-06 feat: add printf switch to lis2mdl
2024-07-07 fix: update topic to design
    [mqtt.c, publish.c]
2024-07-07 feat: add printf debug control to motor
2024-07-07 fix: use proper json for battery drain test
2024-07-07 chore: prep for wireless ota
2024-07-11 fix: update pcb to beta
    - Fix daughter board pin hole size
    - Add better support for connecting J-Link
    - Update silkscreen
    [dancing_duck.kicad_pcb, dancing_duck.kicad_sch]
2024-07-12 feat: add adc
    - add adc for battery and temperature sesnsor.
    - add mqtt publishing for the values
    Tested by injecting voltage directly to ADC pins. Tested temp, showed room temperature. Tested battery voltage, there is an issue here.
    Battery voltage is not being read correctly for high voltages. Hypothesis: gate for 1pf SAR cap not open long enough to charge completely. Will add buffer capacitor to voltage divider output.
    [adc.c, main.c, publish.c]
2024-07-12 fix: add capacitor to pcb
    [dancing_duck.kicad_pcb, dancing_duck.kicad_sch]
2024-07-12 fix: add switch for mirrored props
    [motor.c]
2024-07-12 fix: remove debug printf
    [adc.c]
2024-07-13 feat: add calibration for lis2mdl
2024-07-13 fix: update publish rates
    [publish.c]
2024-07-13 fix: prep for wet run
    need to be able to log into alternative wifi in field
    [main.c, mqtt.c]
2024-07-13 fix: prop mirror
2024-07-14 build: improve scripting - Add wireless OTA script to ensure proper duck gets proper firmware - Move to less used channel on AP - Cleanup Jlink flash files
2024-07-14 fix: increase wifi timeout for
    - needed after dedicated AP and OTA script complete
    [main.c]
2024-07-14 fix: watchdog timeout too long
    shorten to less than 8333ms.
    [config.h]
2024-07-15 feat: add RX to GND solder bridge to PCB
    [dancing_duck.kicad_pcb, dancing_duck.kicad_sch]
2024-07-20 fix: make wifi timeout less than wdt
    [config.h, main.c]
2024-07-20 refactor: prep motor.c for new algos
2024-07-20 feat: add new motor commands
2024-07-23 chore: turnoff motor debugging
2024-07-25 fix: add device_id arg to mag_calibrate
2024-07-26 fix: update watchdog logic
    [main.c]
2024-07-26 chore: add calibration data
2024-07-27 fix: debugger ip changed
    using raspberry pi server now
2024-07-27 fix: remove alt network, add unique mqtt client id
    [config.h, main.c, mqtt.c]
2024-07-27 fix: update calibration of duck 1
    [lis2mdl.c]
2024-07-29 fix: increase point deadbnad
    [motor.c]
2024-07-29 fix: cleanup shared resources
    bug: fixed use of stack variables being passed around as FreeRTOS parameters. Now they are on the heap.
    added: added command to dump motor buffer and immediately turn off motors.
    [commanding.c, main.c, motor.c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]
2024-07-29 fix: improve sync of coordinator and ducks
    [commanding.c, motor.c]
2024-07-30 fix: fix network stability
    [lwipopts.h, publish.c]
2024-07-30 fix: add threadsafe gaurds for lwip calls to mqtt
    [mqtt.c]
2024-07-30 feat: add persistant reboot data
    [main.c, mqtt.c, watchdog.c]
2024-07-31 fix: add missing header
    [publish.c]
2024-07-31 feat: add mqtt publish metrics and reset
    [publish.c]
2024-07-31 fix: shorten mqtt buffer
    we will anlayze metrics in the future to see if this buffer is ever full
    [lwipopts.h]
2024-07-31 refactor: update adc module based on style guide
2024-08-01 feat: add more mqtt reset logic
    [publish.c]
2024-08-01 fix: const pointer in main.c
    [main.c]
2024-08-01 refactor: motor module
2024-08-03 feat: add kasa calibration to motors
2024-08-03 chore: clean up interfaces for magnetometer
2024-08-06 feat: add launch and calibrate commands
2024-08-08 fix: limit max motor consumption
    [config.h, motor.c]
2024-08-08 fix: add 3.3V rail closer to RUN (Jumper together)
    [main.c]
2024-08-08 fix: extend calibration time
    [config.h]
2024-08-10 fix: add lis2mdl reset recovery
    I'm guessing this is caused by EMF, but every once in a while the config registers reset on some of the devices.
    [lis2mdl.c, publish.c]
2024-08-15 fix: bump up mqtt buffer
    [lwipopts.h]
2024-08-17 fix: update rmse limit for noisy environments
    [config.h]
2024-08-20 fix: add mid motor range
    [commanding.c, config.h, motor.c]
2024-08-21 feat: calibration through reset
    anytime there is a soft reset the magnetometer calibration will be saved in watchdog scratch registers.
    bug: fixed semaphore give bug. now only happens once.
    [config.h, motor.c, mqtt.c]
2024-08-21 fix: raise retry count for wifi
    [config.h]
2024-08-21 fix: count sync dances
    the simple prng does not play well with MOD numbers, and we want to keep the sync going across all ducks, so we will just cycle throug the dances. it is unlikely any of the audience will be paying attention long enough to see the pattern.
    [dance_generator.c]
2024-08-22 feat: have launch use swim if calibrated
2024-08-22 fix: update better strtoul and loggin
    [config.h, mqtt.c, publish.c]
2024-08-22 feat: add motor fault counter
2024-08-23 fix: tune up system
    - tune stack sizes for tasks
    - trim excessive printing
    - develop way to check idle times on both cores
    - we are using only a small percentage of CPU
    [config.h, lwipopts.h, main.c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]
2024-08-23 fix: mqtt messaging bug
    [mqtt.c]
2024-08-23 feat: make it so we dance more often
    - if we accidently reset, and we have calibration data, we should start dancing.
    - We don't need to wait for the sync clock. it will find the duck eventually
    [main.c]
2024-08-23 chore: refactor magnetometer for better printing
2024-08-24 feat: add wind correction
    testing: not done on real device yet.
    [commanding.c, config.h, dance_generator.c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]
2024-08-26 fix: wind cli error
    [dance_generator.c, duck_mqtt_cli.py]
2024-08-27 fix: make dances bigger
    [config.h, dance_generator.c]
2024-08-29 fix: update restart limits based on data
    [config.h, publish.c]
